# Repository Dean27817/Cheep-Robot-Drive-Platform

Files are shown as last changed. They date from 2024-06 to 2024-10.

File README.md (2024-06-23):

<h1>$20 Combat Robot Drive Base</h1><br>
this is a project designed to make the world of combat robotics more accessible. It achieves this by lowering costs for the robot to just $20. No expensive controllers or motors. This robot will use a phone connected via Bluetooth as a controller and cheap N20/N10 motors for driving. It uses the esp32-S3-ZERO from Waveshare to connect to the phone and act as a brain to control the H-bridge, which is a basic form of speed controler. This does mean that you will have to upload code, but the code is already written and you need to load it onto the esp32.

<h2>Current big update</h2><br>
This robot has gone into its first fight and has done... OK. I will be using the things that I learned from these fights to upgrade this robot. These upgrades will mostly include the BOM, and a little bit of code. I will upload some videos of the fights soon as well as a better assembly guide.

<h2>assembly</h2>
<h3>Electronics and programming</h3><br>
This project will involve soldering to connect all the components (Listed in the BOM). 

1. You will need a pair of motors. each motor will be soldered to one output on the H-Bridge. make sure both of the black/blue wires are connected to the same channel on the H-bridge to make sure they spin in the same direction. 
2. The red power lead should then be soldered to the switch, and the other end of the switch soldered to the VCC pin on the H-bridge, and the black goes directly to the GND pin.
3. Solder the pins according to the table below
   
   |esp32|H-bridge|
   |-----|--------|
   |5V|VCC|
   |GND|GND|
   |GPIO5|in1|
   |GPIO3|in3|
   |GPIO4|in2|
   |GPIO10|in4|
   
   This is just the way it is in code right now, but you can change it if you solder it differently

4. Upload the code to the ESP32. You will need to install the ESP32Servo Library (Used for the ESP32PWM) and the DabbleESP32 library (used for Bluetooth). Also, make sure to change the name in the Dabble. Begin call in the setup function as this will be the name that will show up in the Bluetooth connection. When you go to upload you will need to make sure that you have installed the ESP32 add-on if you are using the Arduino IDE (tutorial here: https://randomnerdtutorials.com/installing-the-esp32-board-in-arduino-ide-windows-instructions/)

<h3>Chassis</h3><br>
Link to the onshape document: https://cad.onshape.com/documents/b9fa5f2ea41ea05079f2ad30/w/9d92b5062ffe81545ec4d5d4/e/a26d33166ec21f0438be70de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
The chassis for this robot is entirely 3D printed. It is designed as a simple wedge so it is just the wheels and a basic body. I am pretty happy with how the body is. the motors fit into the slots by the holes in the sides and are held in with zip-ties (though also using hot glue is recommended). the wheels have slots for an M2 nut to fit into and have a bolt go through to hold them in place. All of the electronics go in front of the motors (pics coming soon). The TPU wheels work but have very little traction with the floor. The wheel hubs will work with the Lego and TPU wheels, so there is only one model to print.

<h2>TODO</h2><br>
Finish failsafes<br>
Finish assembly guide<br>
Take and upload photos for assembly and electronics<br>
Finish code comments<br>

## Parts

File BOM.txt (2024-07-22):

Just a warning, I baught all of this on amazon, I cant guarentee the ligitimusy or quality of any of the other sources. If any of these are scams, please let me know so I can remove them from this list and find an alternitive

Speed controler
Amazon: https://www.amazon.com/KOOBOOK-DRV8833-Module-Bridge-Controller/dp/B07S4FVY9M/ref=sr_1_5?sr=8-5
Aliexpress: https://www.aliexpress.us/item/3256806258295019.html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

ESP32
Amazon: https://www.amazon.com/waveshare-Development-ESP32-S3FH4R2-Dual-Core-Processor/dp/B0CHSBQ1G4/ref=sr_1_9?sr=8-9
Waveshare (cheeper): https://www.waveshare.com/esp32-s3-zero.htm

Battery
Amazon: https://www.amazon.com/VICMILE-Batteries-Compatible-Holystone-Quadcopter/dp/B0C4NTP1YF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
Dont buy cheap batteries
battery plug
Amazon: https://www.amazon.com/OliYin-Connector-Heatproof-Helicopter-Multicopter/dp/B08H7WZJND/ref=sr_1_1?sr=8-1
Aliexpress: https://www.aliexpress.us/item/2251832841239323.html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

switch
Amazon: https://www.amazon.com/Tnuocke-Vertical-Position-Latching-SS12F15-G5/dp/B099N3HFPG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
Aliexpress: https://www.aliexpress.us/item/2251832626374457.html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

motor
any n10/n20 motor over 500 rpm at 3 volts (1s) should do, just make sure its not too slow.
really, you can use whatever you want. on my model, im using 4, 7mm gearmotors to drive the robot.
the one limit is to make sure that the motor wont pull more that 1.5 amps at 4.7v

Recomended motors:
Amazon: https://www.amazon.com/dp/B0CJ7163G2?ref_=cm_sw_r_apan_dp_Z8YTW53NWPTV1Y20NZB3&starsLeft=1&skipTwisterOG=2
Aliexpress: https://www.aliexpress.us/item/3256806131900144.html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

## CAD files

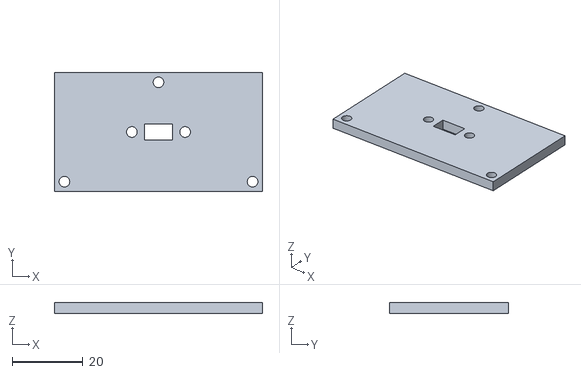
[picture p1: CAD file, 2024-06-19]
STL/chassis - Lid.stl
58.6 x 33.6 x 3.00

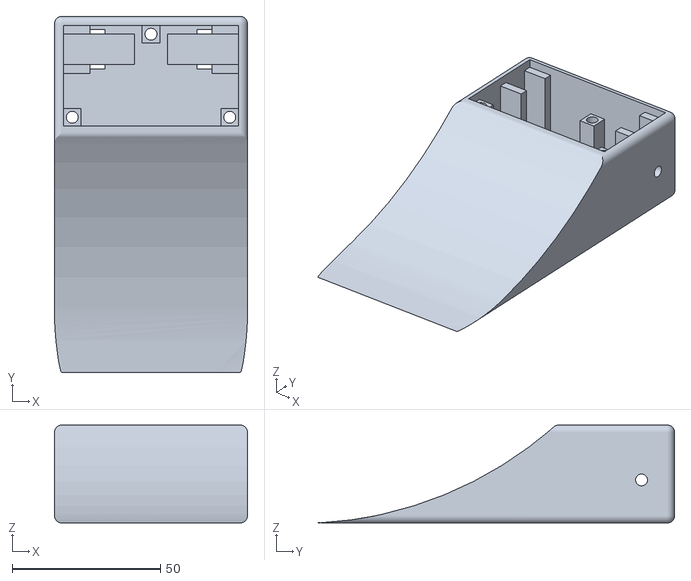
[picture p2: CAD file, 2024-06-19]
STL/chassis - Base.stl
65.0 x 120.0 x 33.0

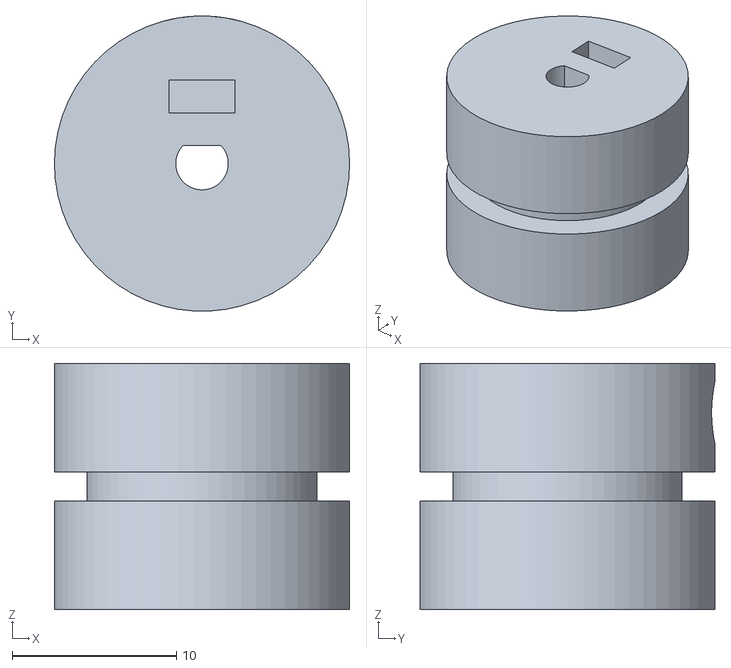
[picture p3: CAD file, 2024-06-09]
STL/Wheel Hub.stl
18.0 x 18.0 x 15.0

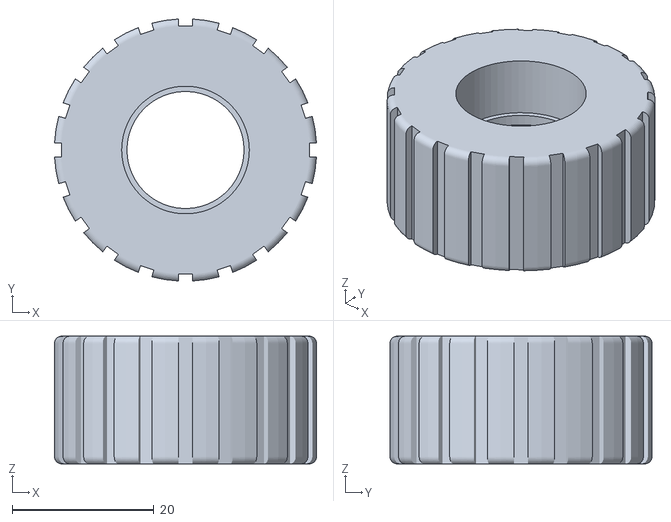
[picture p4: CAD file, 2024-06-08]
STL/replacment wheel.stl
36.9 x 36.9 x 18.0

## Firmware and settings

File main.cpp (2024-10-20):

//cheep robot base
//created by dean morgan
//this code is designed to be used on a esp32-S3-Zero from waveshare
//it uses a basic 2 chanel H-Bridge motor controller, each chanel driving 2 motors with custom printed gearboxes

//defonitions to use the gamepad modual on dabble
#define CUSTOM_SETTINGS
#define INCLUDE_GAMEPAD_MODULE

//basic arduino library
#include <Arduino.h>
//used to allow the user to control the robot with their phone
#include <DabbleESP32.h>
//used to control PWM for the MC
#include <ESP32Servo.h>
//Used to make the speed controller easier to work with
#include "ESC.h"


//define the pins that the inputs of the Motor controller will be solderd to
#define in1 5
#define in2 3
#define in3 4
#define in4 2

//defines the limits of the speeds being sent
#define MIN_SPEED 0 // speed just slow enough to turn motor off
#define MAX_SPEED 2000 // speed where my motor drew 3.6 amps at 12v.

//declaring an ESC object for each "in" pin
ESC Speed1(in1, 0, 3000, 500);
ESC Speed2(in2, 0, 3000, 500);
ESC Speed3(in3, 0, 3000, 500);
ESC Speed4(in4, 0, 3000, 500);

void setup() {
    //used for communication with the computer
    Serial.begin(9600);
    //starts the bluetooth connection
    Dabble.begin("Dean Morgan Drive Base");
    delay(1000);

    //Allow the pins to send electricity out
    pinMode(in1, OUTPUT);
    pinMode(in2, OUTPUT);
    pinMode(in3, OUTPUT);
    pinMode(in4, OUTPUT);

    //prepares the pins for PWM
    Speed1.arm();
    Speed2.arm();
    Speed3.arm();
    //Speed4.arm();
}

void loop() {
  //makes the esp32 reload the input from the phone
  Dabble.processInput();

  //gets the speed values that the left and right wheels should be traveling
  //the multiplication is to take the -7 to 7 value given by dabble and turns it into a usable value to use in the ESC functions
  double Left = (GamePad.getYaxisData() - GamePad.getXaxisData()) * (MAX_SPEED/7);
  double Right = (GamePad.getYaxisData() - GamePad.getXaxisData()) * (MAX_SPEED/7);

  //right wheel forward
  if(Right > 0.2)
  {
    digitalWrite(in1, LOW);
    Speed2.speed(abs(Right));
  }
  //right wheel stop
  else if(Right > -0.2 && Right < 0.2)
  {
    Speed1.stop();
    Speed2.stop();
  }
  //right wheel backwards
  else 
  {
    digitalWrite(in2, LOW);
    Speed1.speed(abs(Right));
  }


  //left wheel forward
  if(Left > 0.2)
  {
    digitalWrite(in3, LOW);
    Speed4.speed(abs(Left));
  }
  //left wheel stop
  else if(Left > -0.2 && Left < 0.2)
  {
    digitalWrite(in3, LOW);
    digitalWrite(in4, LOW);
  }
  //left wheel backwards
  else 
  {
    digitalWrite(in4, LOW);
    Speed3.speed(abs(Left));
  }
  
}

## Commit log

2024-05-03 began intagrating Motor controlls
2024-05-03 PWM issues fixed
    I got get PWM working properly. I think it should work now, but it is untested. currently a fixed value in code.
    [main.cpp]
2024-05-06 changed PWM library to RC_ESC
2024-05-06 added math to add tank drive
    There is still a bug where one side of the drive spins slowly when it shouldn't. will fix soon
    [main.cpp]
2024-05-27 Added code to make the drive actually work
    After too long I found a library that will actually work with these speed controllers. The drive code is in a separate function from the dabble code. just makes it a bit cleaner. Still need to finish the docs, but it works.
    [main.cpp]
2024-05-27 Aedded bill of materials
2024-06-02 Changed up the drive
    Allowed for the reversing of the default motor direction
    [main.cpp]
2024-06-03 Added first models
    [Wheel Hub.stl, chassis - Base.stl, chassis - Lid.stl]
2024-06-08 Added better STL files
    Made the wedge longer to make it not flip over. Also changed around the placement of the electronics to make better weight distribution.
    [Wheel Hub.stl, chassis - Base.stl, chassis - Lid.stl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]
2024-06-08 Changed the failsafes
    started working on adding the failsafe to make the robot stop when not connected. still doesn't work, but wanted to save the attempt
    [main.cpp]
2024-06-08 Update README.md
    Changed chassis description and guide. also added more to the todo list.
2024-06-09 added flush screw holes
    [Wheel Hub.stl]
2024-06-12 electronics housing bigger
    also put the electronics in front of the drive motors to move the wheels back so the robot dosn't do "the thing" as well as stopping the nose lift issue.
    [chassis - Base.stl, chassis - Lid.stl]
2024-06-12 Update README.md
    Changed some of the chassis assembly
2024-06-19 Made the electronics housing bigger
    This makes room for the switch and easier assembly with more space for misc wires
    [chassis - Base.stl, chassis - Lid.stl]
2024-06-22 Temp Pins
    Different pin nums between robots. Will deleate later
2024-06-27 Delete Robot Motor Pos.txt
    Uneccacary
